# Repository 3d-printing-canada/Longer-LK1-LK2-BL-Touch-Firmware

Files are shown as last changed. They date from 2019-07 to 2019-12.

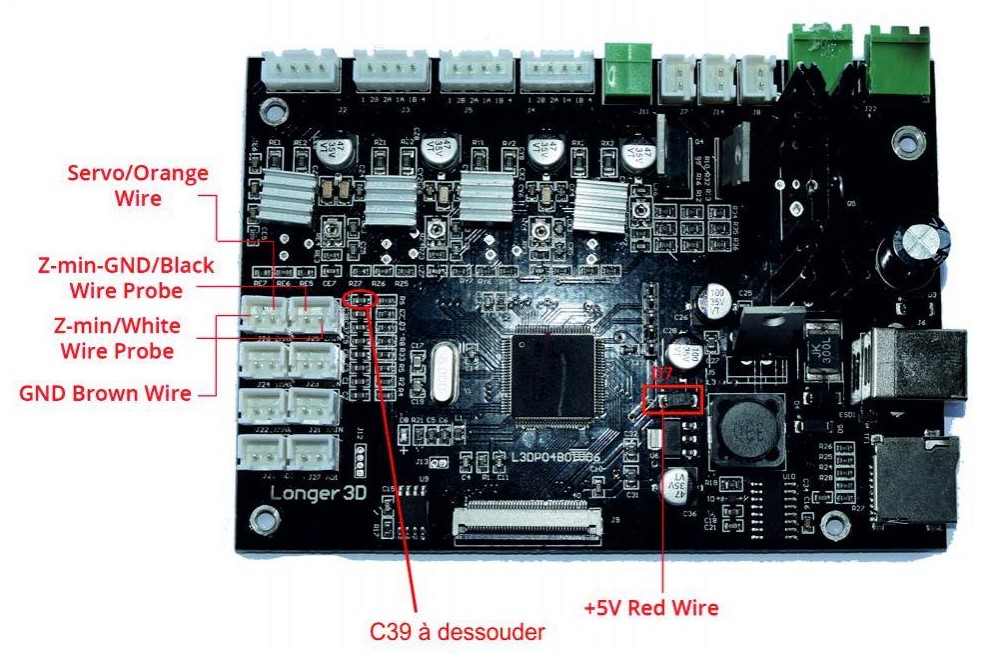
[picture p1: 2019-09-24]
Longer V08, V07, V06 Wiring Diagram BL Touch.jpg

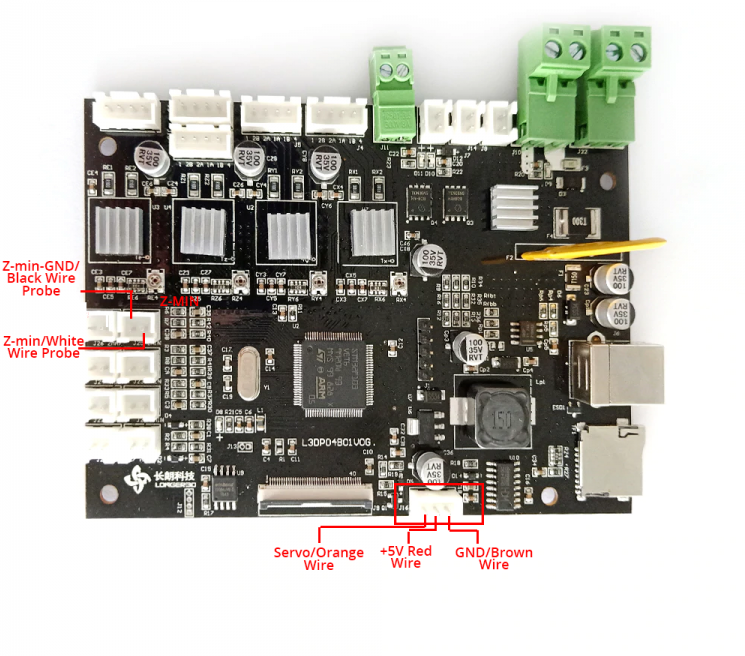
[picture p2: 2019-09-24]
Longer VOG Motherboard Wiring Diagram BL Touch.PNG

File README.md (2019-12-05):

# Longer-LK1-LK2-BL-Touch-Firmware
In this guide we'll show you how to install and upload firmware and hardware for your BL touch on the Longer LK1/LK2. The standard (non BL touch) firmwares have also been uploaded. There are a couple variations of these printers, so there are some important points we need to note to do the conversion successfully: 

### NOTE: Firmwares are no longer named "project.bin" as said in some of the YouTube guides - now they are named after the printer type and motherboard type (i.e. LK1V0G_BLtouch_firmware.bin)

### LK4 USERS: Use the same firmware as the LK2! 

### VOG Vs V08, V07, V06 Motherboards 
The V0G Style motherboard have a handy little connector you can use to plug the BL touch into - not so on the V08 and previous boards. To determine the style of motherboard in your machine, compare it to the images in this github identifying each board. You will have to use the proper firmware for each board, so make sure that you select the correct firmware for both your board type and printer type.  

# Bill Of Materials 
### For Longer LK2 / Alfawise U30 
- Longer LK2 OR Alfawise U30 with V0G Motherboard / Connector (Please see the VOG Motherboard image Above to confirm that you have the correct board)
- BL touch: https://3dprintingcanada.com/products/genuine-antclabs-bltouch-sensor
- EX-1000 Extension Cable (For Longer LK2 / Alfawise U30 V0G MOTHERBOARD ONLY): https://3dprintingcanada.com/products/genuine-antclabs-bltouch-extension-cables
- BL Touch 3D Printed Mount (Uploaded to this repository, but here is the Author): https://www.thingiverse.com/thing:3526108

BUY THE COMPLETE KIT: https://3dprintingcanada.com/products/longer-lk2-alfawise-u30-bl-touch-kit
This kit comes with everything you need for the modification, including a pre-soldered extension cable with integrated resistor

### For Longer LK1 / Alfawise U20 

- BL touch: https://3dprintingcanada.com/products/genuine-antclabs-bltouch-sensor
- SM-XD-1800 Cables https://3dprintingcanada.com/collections/antclabs/products/copy-of-genuine-antclabs-bltouch-extension-cables-sm-xd-1800

# Hardware Installation 

### Requirements for the V0G board
The extension wires must have a 1K 1/8th watt resistor bridging the positive (red) and signal (orange) wires at the motherboard connector for the BL touch (also shown in the wiring diagram). 3D Printing Canada sells the wire pre-soldered with a resistor (for the LK2 only), or you may try it yourself without soldering by sticking one end of the resistor in the top of the connector for each of the wires, securing it with tape. Soldering it to the wires is the best option. I do this by cutting the  red and orange wires about 10cm from the connector at the same place, stripping the ends, and then soldering both red ends and both orange ends to either end of the resistor. Heat shrink to protect the connections. 

### Requirements for the V08, V07 and V06 boards
The following modifications must be made for the VO8, V07 and V06 boards: 

1) Using your clippers you must clip off the unused 3rd pin of the 3 pin JST-XH (white) connector for the Z probe min signal (if using the 1800mm cables). That will allow you to insert the connector into the right slot when interfacing the BL touch on the motherboar.
2) Remove the red (+5V) wire from the black 3 pin JST connector, put the brown and orange ones together, and then clip off the unused 3rd pin on the black JST connector to make a 2 pin (or use one of the blank 2 pin connectors that come with the BL touch). 
3) Remove / desolder capacitor C29 on the motherboard as marked in the wiring diagram - this can be done with a soldering iron or very carefully by twisting it off with needle nose pliers. 
4) Solder the red +5V wire of the BL touch to the D7 capacitor as shown on the wiring diagram. 

### Hardware Installation Procedure 
1) Print and mount your BL touch, no springs required, using the 3D printed Mount. 
2) Connect your BL touch leads to the correct pins on the motherboard as indicated in the wiring diagram. 
3) Carefully route the BL touch wires through the existing cable management system for the hotend wires.

### Software Installation (For Standard & BL Touch Firmwares)
1) In the main folder you will see a '####_firmware.bin' file. Copy that folder onto your SD card and insert it into the printer. Turn the printer on and watch it upload. 
2) When you see the main info screen for marlin appear, turn the printer off. Insert your SD card into your computer again and delete '####_firmware.bin' (failure to do this will mean the firmware will reflash every time). IMPORTANT: You will notice there is now an EEPROM.dat file. DO NOT delete this - as it serves as the Eeprom for your printer (the memory).
3) Re-insert your SD card

## Configuring the BL Touch
NOTES:
i) To navigate to a previous menu, you have to scroll to the top of your current menu and press the topmost option 
ii) The EEPROM data for the Z probe offset is stored on the SD card. If you start the printer without the SD card in it, that setting will not load properly. Always start your printer with the SD card in it. 

1) Turn on your printer. You will notice you have three controls: two blue navigation arrows and a red select button. 
2) Press the select button and use the arrows to nativage to 'Temperature'.
3) Select 'Preheat PLA' from the list, then 'Preheat PLA' from the next menu. This will preheat the printer.
4) Press the select button and use the arrows to navigate to 'Motion'.
5) Select 'Auto Home'. The printer should home and end up in the center of the bed.
6) In the 'Motion' menu, select Move Axis > Move Z > 10mm. Move the axis down until it is at +000.0 mm. 
7) Navigate to the main menu. Go to Configuration > Probe Z offset
8) Put a piece of paper under the nozzle. Move it back and fourth continuously. Press the blue down button and the gantry will slowly start to move down. You may keep your finger on the button. 
9) Once the nozzle grips the paper enough that it makes a little resistance, but the paper can still move, press the red select button. Scroll down in the 'Configuration' menu until you reach 'Store Settings'. Select that a couple times just to be sure. You're done! 

## Configuring Cura

Cura configuration is the same as the Ender 3 cura config - please refer to our video below for the procedure: 
https://youtu.be/dRgWrepDUBE?t=1316

Please note: The Ender 3 configuration will work for the LK2, but for the LK1 you should select the "CR-10" default profile and add a G29 to it as per the instructions in the Ender 3 cura config video above.

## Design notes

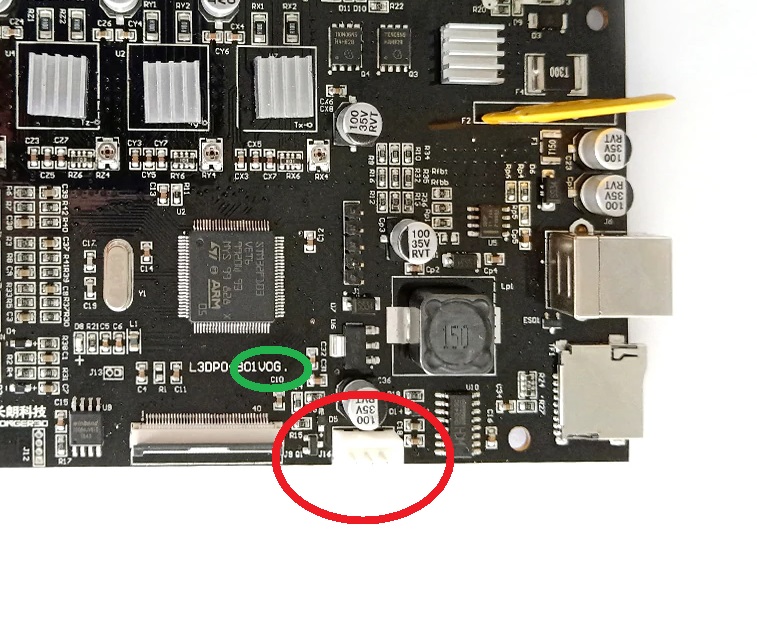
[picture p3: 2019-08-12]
Longer Motherboard Identification.jpg

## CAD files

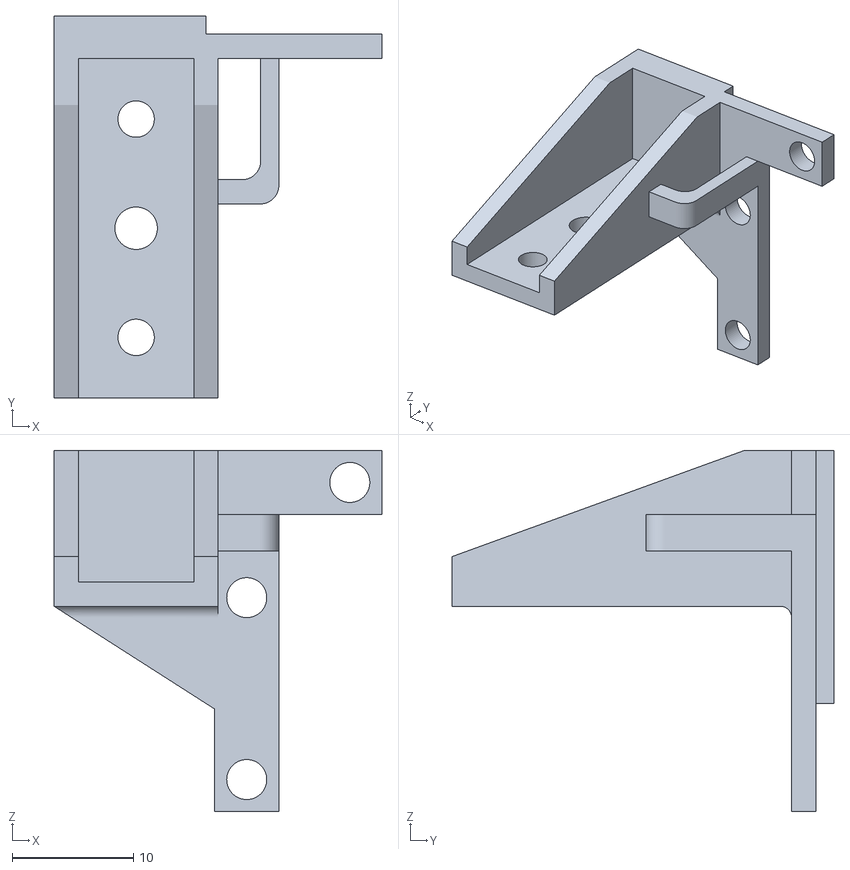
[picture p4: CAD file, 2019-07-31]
BLTouch_mount_for_Alfawise_U20_U30/files/bltouch_mount_Alfawise_U20.stl
27.0 x 31.5 x 29.8

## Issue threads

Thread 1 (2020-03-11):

LK4 Pro BL Touch

mrv96, 2020-03-11:
Hi, does the hardware part of your tutorial work for the Longer LK4 Pro? In particular, is the 1k resistor needed?

Have you some suggestions in order to install the BL Touch on the LK4 Pro?

RokHed19, 2020-06-15:
I might suggest you use the Marlin source and firmware from the official Longer website as a starting point.

mrv96, 2020-06-15:
For what concern the software part i've no problem, i would need to know if i have to do something related to the hardware.

RokHed19, 2020-06-15:
Longer Already has a working version of Marlin for the LK4 pro on their website, including source code. You don't need to do anything to the hardware. It already runs Marlin.

DougKDavis, 2022-07-09:
Is there a working version of Marlin for the LK5 pro on Longer website, including source code for the BLTouch V3.1?
I am having problems getting the firmware for the BLTouch to work on my Longer LK5 Pro.

DougKDavis, 2022-07-09:
Actually,  not sure what is the source code or what this is for?
I get the firmware but do not know what is meant by source code.
Thank you

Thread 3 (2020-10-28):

Problem with touchscreen after Firmware

chriscarreiro1, 2020-10-28:
After getting the firmware loaded; Marlin screen loads up but the touchscreen is not functioning. I have a Lk1 with the 0G board installed. and the Resistor is attached between the wire for the BLTouch.

Grayrider2500, 2020-12-09:
I have the same issue as chriscarreiro1, but on an LK4. After I get the firmware loaded, the Marlin screen loads up but the touchscreen is not functional. I have the V0G board and the resister is attached between the correct wires. I also had to rename the .bin file to project.bin to get the firmware to load.

Grayrider2500, 2020-12-09:
*****Solved*****

Referencing my above comment: After further troubleshooting, I discovered if I carefully pressed around the LCD display after installing the correct firmware, it would eventually press the return button, though not in the correct location. That allowed me into the menu system of the firmware. Further probing allowed me to eventually locate the location of the other misaligned buttons and eventually I located the screen calibration, under the calibrate menu, which then corrected the issue. It is then imperative to save the configuration, so that the next time you turn on the printer, the LCD works properly or you will have to recalibrate the screen again. I hope this helps.

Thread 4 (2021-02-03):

u30 V08 BLTOUCH DOESN'T WORK

ThePsyk8, 2021-02-03:
Hello,
I think there was an error to compile the firmware for V08 motherboard. I would like recompile it but my visual studio tell me FAILED.
The U20 V08 works, but her dimensions on U30 create problems during bed levelling. Can you recompile it? Help me please
Thanks for all

ks56686, 2021-02-04:
I'm still trying to figure that out myself it could be a problem in the slicing software in Cura that's what I'm thinking I would try cr/10 that may work possibly

Get Outlook for Android<https://aka.ms/ghei36>

________________________________
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

ThePsyk8, 2021-02-04:
It's not a problem of slicing, because in all other version for V08(example
U20 V08) when I digit G28 from Pronterface the bltouch works. So I believe
the problem is the incomplete configuration in
\pins\stm32\pins_LONGER3D_LK.h:

//#define SERVO0_PWM_OD
//#define SERVO0_PIN PD13 // Open drain PWM pin on the V0G (GND or floating 5V)

#define SERVO0 _PIN PE5 // Pulled up PWM pin on the V08 (3.3V or 0)

Thanks

Il gio 4 feb 2021, 01:56 ks56686 <notifications@github.com> ha scritto:

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

ks56686, 2021-02-04:
I'm going to look into that more to see what's going on I'll let you know about it

Get Outlook for Android<https://aka.ms/ghei36>

________________________________
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

ThePsyk8, 2021-02-04:
Ok thanks

Screambear, 2021-03-24:
Hello,

I have the same problems like ThePsyk8.

When i flash the Compiles File LK2V08_BLtouch_firmware.bin the BLTouch doesnt work. When I flash the file LK1V08_BLtouch_firmware.bin it works. But the dimensions arent like the U30/LK2. Please help

Lucker1981, 2023-01-21:
hi
 i have the same problem. How i can get the Bedmasurement on 220x220?

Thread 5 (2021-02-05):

V0G BL touch not working

96ramctd, 2021-02-05:
Just installed the touch on Longer LK1 and have no control over BL touch or bed leveling with the LK1 V0G bltouch .bin file.  Installed LK1 plus V0G .bin and everything operates as it should but only runs the sensor over left front 2/3 of the bed.  Slowly learning VS Code but mechanical parts are my forte so haven't been able to muddle my way through compiling the .bin file that I edited. Any assistance would be greatly appreciated.

ks56686, 2021-02-06:
I don't know nothing about alk1

Get Outlook for Android<https://aka.ms/ghei36>

________________________________
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

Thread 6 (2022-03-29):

Where to find the standard (non BL touch) firmwares

Evercond, 2022-03-29:

Evercond, 2022-03-29:
Readme says "The standard (non BL touch) firmwares have also been uploaded." But I can not find it. Tryed to compile the source with no BL Touch defined, it failed. I just want to add linear advance to my cheap LK-1, but none of provided firmwares support it, and this one can not work without BL Touch. Tell me please, where are compiled binaries for non-BLTouch firmware, and does they provide linear advance setting? Or i need custom motherboard?

P.S. Made the Stealthburner extruder for LK-1, and can not test it yet, if you help, I will test it and upload it on thingiverse.

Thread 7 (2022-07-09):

LONGER LK5 Pro With BLTouch

DougKDavis, 2022-07-09:
Is there a working version of Marlin for the LK5 pro on Longer website, including source code (Ido not know what is meant by this sourse code or what it is)for the BLTouch V3.1?
I am having problems getting the firmware for the BLTouch to work on my Longer LK5 Pro.
I hope to be able to use the color touch screen after flashing the new firmware.

DougKDavis, 2022-07-10:
On the Pro Longer boards, there is no need to use a Jumper resistor. I have a Longer LK5 Pro but I could use a Firmware which I could set the off sets for the hotend and the BLTouch Probe.

DougKDavis, 2022-07-10:
My Mother board does not say anything about a a V0G V08, In BIG letters across the board it says, LGT_KIT_V1.0
Any Firmware out there for this board foir the BLTouch where I can set the off sets for the BLTouch and nozzle?

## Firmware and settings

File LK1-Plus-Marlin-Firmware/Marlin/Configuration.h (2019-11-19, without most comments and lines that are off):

#pragma once
#define CONFIGURATION_H_VERSION 020000
#define U30
#define LCD_READ_ID     0xD3   // Read display identification information in reg ID4 0xD3, for ILI9341 screens
#define TS_V12
#define STRING_CONFIG_H_AUTHOR "Hobi, tpruvot"  // Who made the changes.
#define SHOW_BOOTSCREEN
#define STRING_SPLASH_LINE1 SHORT_BUILD_VERSION // will be shown during bootup in line 1
#define STRING_SPLASH_LINE2 WEBSITE_URL         // will be shown during bootup in line 2
#define CUSTOM_STATUS_SCREEN_IMAGE
#define SERIAL_PORT 1
#define SERIAL_PORT_2 2
#define NUM_SERIAL 2
#define BAUDRATE 250000
  #define MOTHERBOARD BOARD_LONGER3D_LK
#define CUSTOM_MACHINE_NAME "3DPC Longer Ready"
#define EXTRUDERS 1
#define DEFAULT_NOMINAL_FILAMENT_DIA 1.75
#define POWER_SUPPLY 0
#define TEMP_SENSOR_0 1
#define TEMP_SENSOR_1 0
#define TEMP_SENSOR_2 0
#define TEMP_SENSOR_3 0
#define TEMP_SENSOR_4 0
#define TEMP_SENSOR_5 0
#define TEMP_SENSOR_BED 1
#define TEMP_SENSOR_CHAMBER 0
#define DUMMY_THERMISTOR_998_VALUE 25
#define DUMMY_THERMISTOR_999_VALUE 100
#define MAX_REDUNDANT_TEMP_SENSOR_DIFF 10
#define TEMP_RESIDENCY_TIME     10  // (seconds) Time to wait for hotend to "settle" in M109
#define TEMP_WINDOW              1  // (°C) Temperature proximity for the "temperature reached" timer
#define TEMP_HYSTERESIS          3  // (°C) Temperature proximity considered "close enough" to the target
#define TEMP_BED_RESIDENCY_TIME 10  // (seconds) Time to wait for bed to "settle" in M190
#define TEMP_BED_WINDOW          1  // (°C) Temperature proximity for the "temperature reached" timer
#define TEMP_BED_HYSTERESIS      3  // (°C) Temperature proximity considered "close enough" to the target
#define HEATER_0_MINTEMP   5
#define HEATER_1_MINTEMP   5
#define HEATER_2_MINTEMP   5
#define HEATER_3_MINTEMP   5
#define HEATER_4_MINTEMP   5
#define HEATER_5_MINTEMP   5
#define BED_MINTEMP        5
#define HEATER_0_MAXTEMP 275
#define HEATER_1_MAXTEMP 275
#define HEATER_2_MAXTEMP 275
#define HEATER_3_MAXTEMP 275
#define HEATER_4_MAXTEMP 275
#define HEATER_5_MAXTEMP 275
#define BED_MAXTEMP      150
#define PIDTEMP
#define BANG_MAX 255     // Limits current to nozzle while in bang-bang mode; 255=full current
#define PID_MAX BANG_MAX // Limits current to nozzle while PID is active (see PID_FUNCTIONAL_RANGE below); 255=full current
#define PID_K1 0.95      // Smoothing factor within any PID loop
  #define PID_FUNCTIONAL_RANGE 10 // If the temperature difference between the target temperature and the actual temperature
  #define DEFAULT_Kp 17.22
  #define DEFAULT_Ki 1.00
  #define DEFAULT_Kd 74.22
#define PIDTEMPBED
#define MAX_BED_POWER 255 // limits duty cycle to bed; 255=full current
  #define DEFAULT_bedKp 338.46
  #define DEFAULT_bedKi 63.96
  #define DEFAULT_bedKd 447.78
#define PREVENT_COLD_EXTRUSION
#define EXTRUDE_MINTEMP 170
#define PREVENT_LENGTHY_EXTRUDE
#define EXTRUDE_MAXLENGTH 200
#define THERMAL_PROTECTION_HOTENDS // Enable thermal protection for all extruders
#define THERMAL_PROTECTION_BED     // Enable thermal protection for the heated bed
#define USE_XMIN_PLUG
#define USE_YMIN_PLUG
#define USE_ZMIN_PLUG
#define X_MIN_ENDSTOP_INVERTING true // set to true to invert the logic of the endstop.
#define Y_MIN_ENDSTOP_INVERTING true // set to true to invert the logic of the endstop.
#define Z_MIN_ENDSTOP_INVERTING true // set to true to invert the logic of the endstop.
#define X_MAX_ENDSTOP_INVERTING true // set to true to invert the logic of the endstop.
#define Y_MAX_ENDSTOP_INVERTING true // set to true to invert the logic of the endstop.
#define Z_MAX_ENDSTOP_INVERTING true // set to true to invert the logic of the endstop.
#define Z_MIN_PROBE_ENDSTOP_INVERTING false // set to true to invert the logic of the probe.
#define X_DRIVER_TYPE  A4988
#define Y_DRIVER_TYPE  A4988
#define Z_DRIVER_TYPE  A4988
#define E0_DRIVER_TYPE A4988
#define ENDSTOP_INTERRUPTS_FEATURE
#define DEFAULT_AXIS_STEPS_PER_UNIT   { 80, 80, 400, 98 }
#define DEFAULT_MAX_FEEDRATE          { 200, 200, 100, 25 }
#define DEFAULT_MAX_ACCELERATION      { 500, 500, 100, 1000 }
#define DEFAULT_ACCELERATION          500    // X, Y, Z and E acceleration for printing moves
#define DEFAULT_RETRACT_ACCELERATION  500    // E acceleration for retracts
#define DEFAULT_TRAVEL_ACCELERATION   1000    // X, Y, Z acceleration for travel (non printing) moves
  #define DEFAULT_XJERK 10.0
  #define DEFAULT_YJERK 10.0
  #define DEFAULT_ZJERK  0.4
#define DEFAULT_EJERK    5.0  // May be used by Linear Advance
#define Z_MIN_PROBE_USES_Z_MIN_ENDSTOP_PIN
#define BLTOUCH
  #define BLTOUCH_FORCE_5V_MODE
#define X_PROBE_OFFSET_FROM_EXTRUDER -35  // X offset: -left  +right  [of the nozzle]
#define Y_PROBE_OFFSET_FROM_EXTRUDER -5.5  // Y offset: -front +behind [the nozzle]
#define Z_PROBE_OFFSET_FROM_EXTRUDER 0   // Z offset: -below +above  [the nozzle]
#define MIN_PROBE_EDGE 10
#define XY_PROBE_SPEED 8000
#define Z_PROBE_SPEED_FAST HOMING_FEEDRATE_Z
#define Z_PROBE_SPEED_SLOW (Z_PROBE_SPEED_FAST / 2)
#define Z_CLEARANCE_DEPLOY_PROBE   10 // Z Clearance for Deploy/Stow
#define Z_CLEARANCE_BETWEEN_PROBES  5 // Z Clearance between probe points
#define Z_CLEARANCE_MULTI_PROBE     5 // Z Clearance between multiple probes
#define Z_PROBE_LOW_POINT          -2 // Farthest distance below the trigger-point to go before stopping
#define Z_PROBE_OFFSET_RANGE_MIN -20
#define Z_PROBE_OFFSET_RANGE_MAX 20
#define X_ENABLE_ON 0
#define Y_ENABLE_ON 0
#define Z_ENABLE_ON 0
#define E_ENABLE_ON 0 // For all extruders
#define DISABLE_X false
#define DISABLE_Y false
#define DISABLE_Z false
#define DISABLE_E false             // For all extruders
#define DISABLE_INACTIVE_EXTRUDER   // Keep only the active extruder enabled
#define INVERT_X_DIR true
#define INVERT_Y_DIR false
#define INVERT_Z_DIR true
#define INVERT_E0_DIR false
#define INVERT_E1_DIR false
#define INVERT_E2_DIR false
#define INVERT_E3_DIR false
#define INVERT_E4_DIR false
#define INVERT_E5_DIR false
#define X_HOME_DIR -1
#define Y_HOME_DIR -1
#define Z_HOME_DIR -1
#define X_BED_SIZE 400
#define Y_BED_SIZE 400
#define Z_MACHINE_MAX 500
#define X_MIN_POS 0
#define Y_MIN_POS 0
#define Z_MIN_POS 0
#define X_MAX_POS X_BED_SIZE
#define Y_MAX_POS Y_BED_SIZE
#define Z_MAX_POS Z_MACHINE_MAX
#define MIN_SOFTWARE_ENDSTOPS
  #define MIN_SOFTWARE_ENDSTOP_X
  #define MIN_SOFTWARE_ENDSTOP_Y
  #define MIN_SOFTWARE_ENDSTOP_Z
#define MAX_SOFTWARE_ENDSTOPS
  #define MAX_SOFTWARE_ENDSTOP_X
  #define MAX_SOFTWARE_ENDSTOP_Y
  #define MAX_SOFTWARE_ENDSTOP_Z
#define FILAMENT_RUNOUT_SENSOR
  #define NUM_RUNOUT_SENSORS   1     // Number of sensors, up to one per extruder. Define a FIL_RUNOUT#_PIN for each.
  #define FIL_RUNOUT_INVERTING true  // set to true to invert the logic of the sensor.
  #define FILAMENT_RUNOUT_SCRIPT "M600"
#define AUTO_BED_LEVELING_BILINEAR
  #define ENABLE_LEVELING_FADE_HEIGHT
  #define SEGMENT_LEVELED_MOVES
  #define LEVELED_SEGMENT_LENGTH 5.0 // (mm) Length of all segments (except the last one)
  #define GRID_MAX_POINTS_X 5
  #define GRID_MAX_POINTS_Y GRID_MAX_POINTS_X
#define LEVEL_BED_CORNERS
  #define LEVEL_CORNERS_INSET 30    // (mm) An inset for corner leveling
  #define LEVEL_CORNERS_Z_HOP  4.0  // (mm) Move nozzle up before moving between corners
  #define LEVEL_CORNERS_HEIGHT 0.0  // (mm) Z height of nozzle at leveling points
  #define LEVEL_CENTER_TOO        // Move to the center after the last corner
#define Z_SAFE_HOMING
  #define Z_SAFE_HOMING_X_POINT ((X_BED_SIZE) / 2)    // X point for Z homing when homing all axes (G28).
  #define Z_SAFE_HOMING_Y_POINT ((Y_BED_SIZE) / 2)    // Y point for Z homing when homing all axes (G28).
#define HOMING_FEEDRATE_XY (80*60)
#define HOMING_FEEDRATE_Z  (4*60)
#define VALIDATE_HOMING_ENDSTOPS
#define EEPROM_SETTINGS       // Persistent storage with M500 and M501
#define EEPROM_CHITCHAT       // Give feedback on EEPROM commands. Disable to save PROGMEM.
#define HOST_KEEPALIVE_FEATURE        // Disable this if your host doesn't like keepalive messages
#define DEFAULT_KEEPALIVE_INTERVAL 2  // Number of seconds between "busy" messages. Set with M113.
#define BUSY_WHILE_HEATING            // Some hosts require "busy" messages even during heating
#define PREHEAT_1_LABEL       "PLA"
#define PREHEAT_1_TEMP_HOTEND 200
#define PREHEAT_1_TEMP_BED     60
#define PREHEAT_1_FAN_SPEED     0 // Value from 0 to 255
#define PREHEAT_2_LABEL       "ABS"
#define PREHEAT_2_TEMP_HOTEND 250
#define PREHEAT_2_TEMP_BED    100
#define PREHEAT_2_FAN_SPEED     0 // Value from 0 to 255
#define NOZZLE_PARK_FEATURE
  #define NOZZLE_PARK_POINT { (X_MIN_POS + 10), (Y_MAX_POS - 10), 20 }
  #define NOZZLE_PARK_XY_FEEDRATE 100   // (mm/s) X and Y axes feedrate (also used for delta Z axis)
  #define NOZZLE_PARK_Z_FEEDRATE 5      // (mm/s) Z axis feedrate (not used for delta printers)
#define PRINTJOB_TIMER_AUTOSTART
#define LCD_LANGUAGE en
#define DISPLAY_CHARSET_HD44780 JAPANESE
#define LCD_INFO_SCREEN_STYLE 0
#define SDSUPPORT
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

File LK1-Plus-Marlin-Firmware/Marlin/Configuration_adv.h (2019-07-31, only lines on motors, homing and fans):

#define E0_AUTO_FAN_PIN -1
#define E1_AUTO_FAN_PIN -1
#define E2_AUTO_FAN_PIN -1
#define E3_AUTO_FAN_PIN -1
#define E4_AUTO_FAN_PIN -1
#define E5_AUTO_FAN_PIN -1
#define CHAMBER_AUTO_FAN_PIN -1
#define X_HOME_BUMP_MM 5
#define Y_HOME_BUMP_MM 5
#define Z_HOME_BUMP_MM 2
#define HOMING_BUMP_DIVISOR { 2, 2, 4 }  // Re-Bump Speed Divisor (Divides the Homing Feedrate)
#define MICROSTEP_MODES { 16, 16, 16, 16, 16, 16 } // [1,2,4,8,16]
#define DIGIPOT_I2C_MOTOR_CURRENTS { 1.0, 1.0, 1.0, 1.0, 1.0, 1.0, 1.0, 1.0 }  //  AZTEEG_X3_PRO
  #define BABYSTEP_WITHOUT_HOMING
#define ADVANCED_PAUSE_FEATURE
  #define ADVANCED_PAUSE_PURGE_FEEDRATE        3  // (mm/s) Extrude feedrate (after loading). Should be slower than load feedrate.
  #define ADVANCED_PAUSE_PURGE_LENGTH         25  // (mm) Length to extrude after loading.
  #define ADVANCED_PAUSE_RESUME_PRIME          0  // (mm) Extra distance to prime nozzle after returning from park.

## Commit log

2019-07-31 Upload Initial Files
    [Configuration.h, Configuration_adv.h]
2019-07-31 Initial Upload
    [Configuration.h, Configuration_adv.h]
2019-07-31 Wiring Diagram & STL Upload
    [bltouch_mount_Alfawise_U20.stl]
2019-08-12 Upload Standard Firmwares
    [Configuration.h, Configuration_adv.h]
2019-08-14 Modify Servo Pin For BL Touch
2019-09-15 Created compatibility for multiple motherboards
    [Configuration.h, Configuration_adv.h]
2019-09-24 Upload schematics
2019-09-24 New Upload
    [Configuration.h, Configuration_adv.h]
2019-09-26 Recompile firmware
    [Configuration.h, Configuration_adv.h]
2019-11-19 LK1 Plus
    [Configuration.h, Configuration_adv.h]

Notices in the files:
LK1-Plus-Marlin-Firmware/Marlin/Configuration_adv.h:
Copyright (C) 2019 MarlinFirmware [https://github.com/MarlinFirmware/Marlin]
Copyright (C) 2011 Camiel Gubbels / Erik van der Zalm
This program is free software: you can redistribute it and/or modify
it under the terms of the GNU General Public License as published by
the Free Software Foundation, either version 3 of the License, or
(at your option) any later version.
